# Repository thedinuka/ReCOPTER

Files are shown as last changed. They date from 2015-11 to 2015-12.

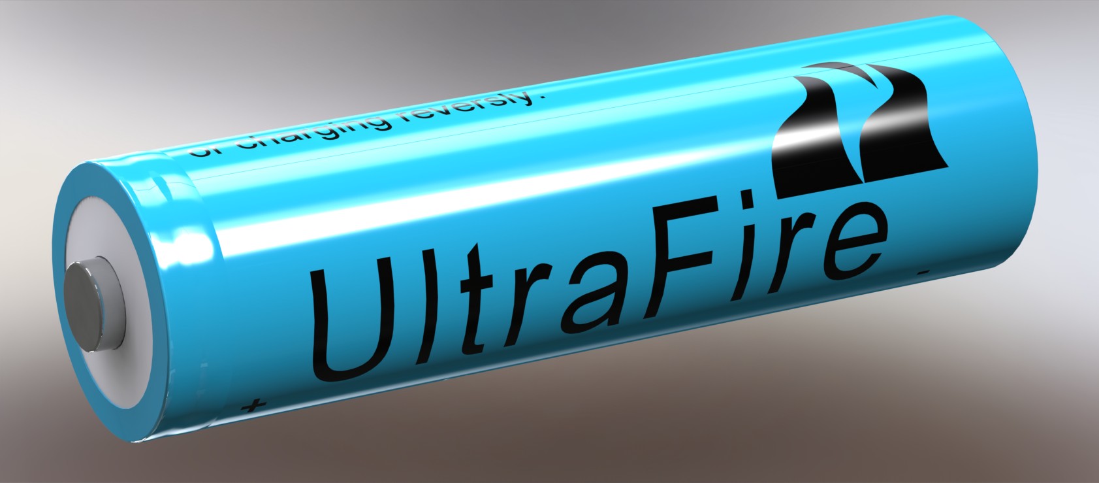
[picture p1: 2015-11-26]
Hardware/Frame/CAD/Parts/ultrafire-18650-2400mah-batteries-1/18650LithiumBatt_Render2.JPG

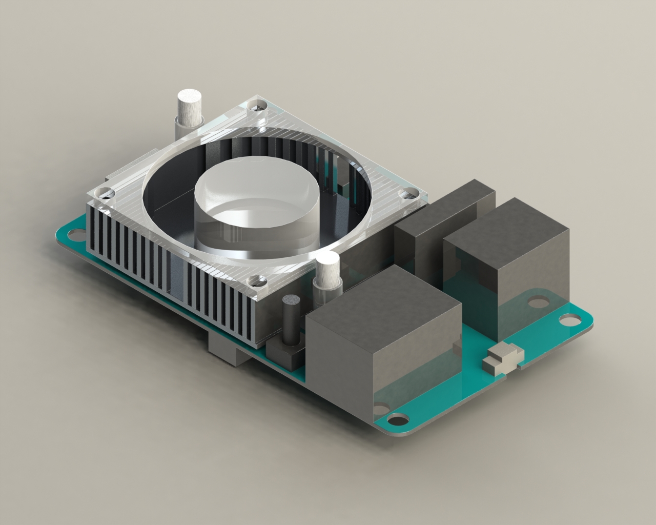
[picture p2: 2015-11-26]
Hardware/Frame/CAD/Parts/Odroid U3/Renderings/odroid-u3.JPG

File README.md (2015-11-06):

# ReCOPTER
Source files for the ReCOPTER paper published in ACRA 2015

If you make use of the material here, please cite the following paper, a copy of which is provided here.
Dinuka Abeywardena, Paul Pounds, David Hunt, and Gamini Dissanayake. Design and Development of ReCOPTER: An Open source ROS-based Multi-rotor Platform for Research. Australasian Conference on Robotics and Automation (ACRA) 2015.

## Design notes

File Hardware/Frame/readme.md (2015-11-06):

This folder contains the CAD models and other relevant design files for the frame of ReCOPTER version 1 as described and illustrated in the ACRA paper.

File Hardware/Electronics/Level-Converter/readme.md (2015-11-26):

Schematics and board files for the level converter board used to communicated between the Pixhawk and the Odroid U3.

The schematics and boad files were prepared using the open source electronics design automation suite KiCad. KiCad is available for download at http://kicad-pcb.org/

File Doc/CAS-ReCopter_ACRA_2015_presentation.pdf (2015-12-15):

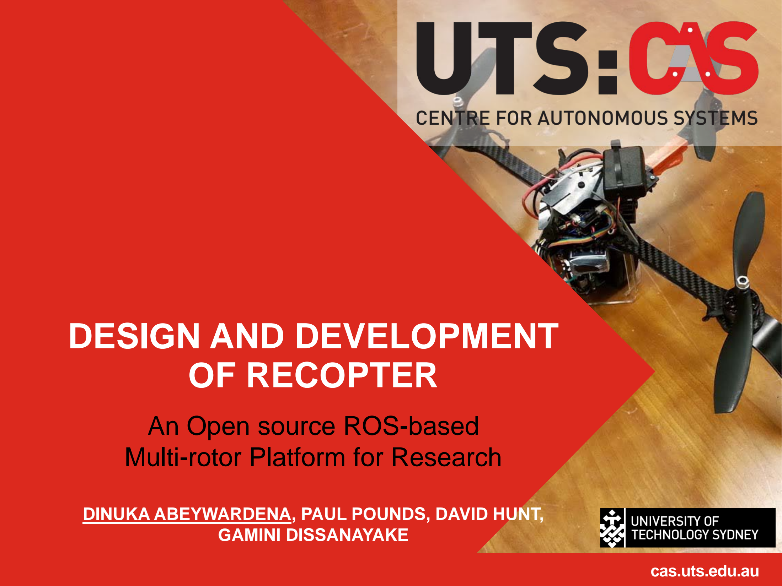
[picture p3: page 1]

# DESIGN AND DEVELOPMENT OF RECOPTER

cas.uts.edu.au

## An Open source ROS-based Multi-rotor Platform for Research

DINUKA ABEYWARDENA, PAUL POUNDS, DAVID HUNT, GAMINI DISSANAYAKE

# MOTIVATION

## Want a UAS to conduct multi-copter research?

## Buy a COTS platform

Expensive
Proprietary hardware and software
Lead time for replacements (specially in Australia!!)

## Build one from Scratch

Time consuming
Can be expensive as well
Requires a diverse skill set

# MOTIVATION

## Want a UAS to conduct multi-copter research?

## Build one based on a proven open source blueprint

Fully customizable HW and SW
Minimum design iterations
Less expensive than COTS Research UAS Easily repairable
Quicker and Easier to build

# APPROACH

Evaluate the state-of-the-art
Evaluate some of the commonly used multi-copter platforms for research
Identify shortcomings & propose improvements Propose design specifications for “researcher friendly” multi-copter design
Design, implement and test and improve Provide a blueprint for the novel design
Build and test multi-copters according to the blueprint Disseminate
Publish results
Open-source the design

# EVALUATE THE S-O-T-A

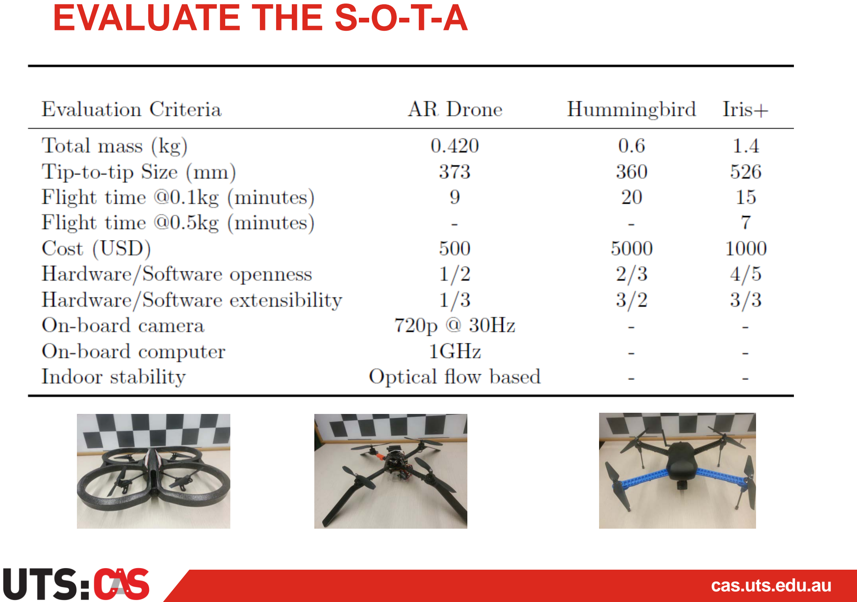
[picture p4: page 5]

# DESIGN SPECIFICATIONS

Criteria | Condition
MTWO | < 2kg
Tip-to-tip size | < 500mm
Max Payload | > 0.5kg
Flight time (0.1kg payload) | > 30 minutes
Flight time (0.5kg payload) | > 20 minutes
Cost | < 1500USD
Openness | Fully open source HW & SW
Extensibility | Modular HW, Standard SW + interfaces
Indoor Stability | Either through optical flow or Tags

# DESIGN PROCESS – FRAME

< ~ 8 inches

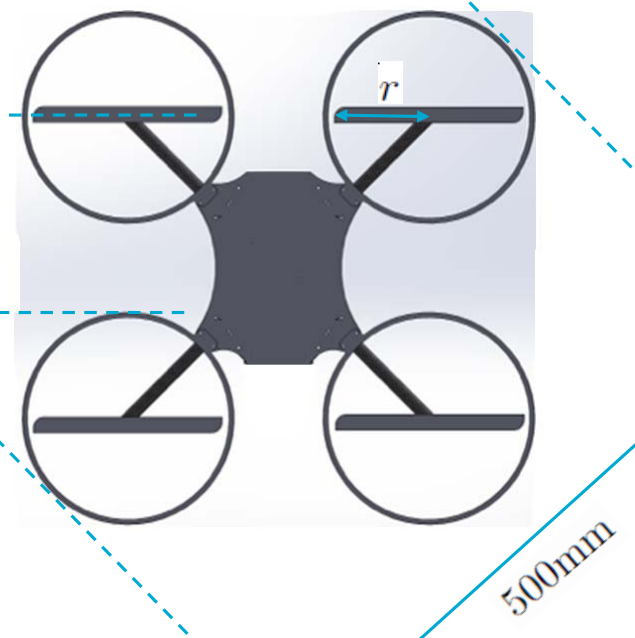
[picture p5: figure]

COTS propeller
options

# DESIGN PROCESS – THRUSTERS AND BATTERY SELECTION

Propellers – T-Motor Carbon Fiber (6, 7, 8 inches)

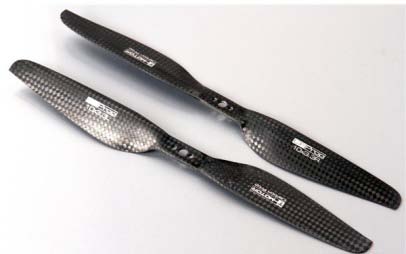
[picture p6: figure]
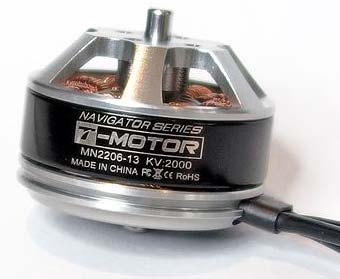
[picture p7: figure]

Motors – Matching T-Motor motors capable of providing at least 5N thrust with any one of the selected propellers (MN 2206 and MT2208)

Batteries – high discharge Li-Ion

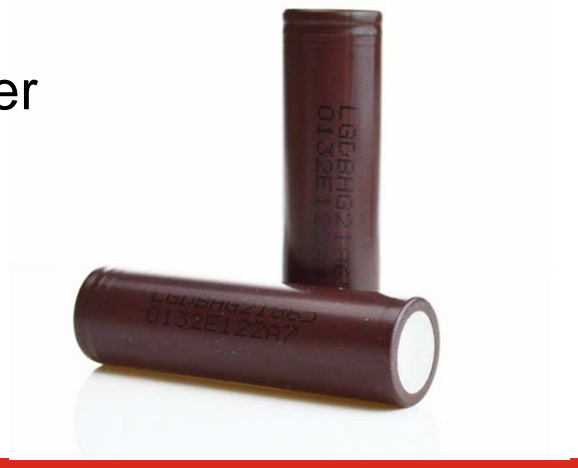
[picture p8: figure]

(compatible configurations with selected Motor/Propeller combinations include 2S2P, 3S2P, 3S3P, 4S3P)

# DESIGN PROCESS – THRUSTERS AND BATTERY COMPARISON

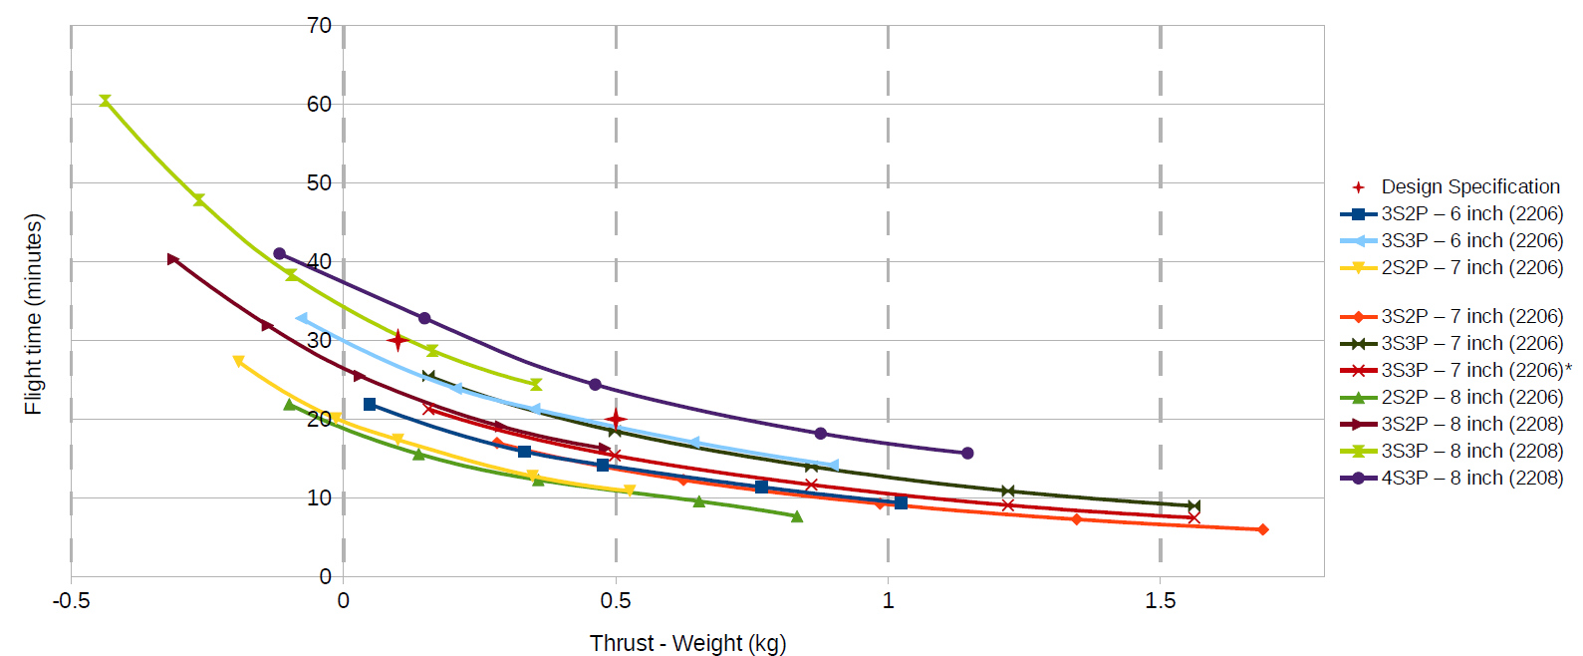
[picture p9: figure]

Data from experimental results obtained from http://www.rctigermotor.com

# AVIONICS + SOFTWARE

Auto-pilot – Pixhawk with native Pixhawk flight stack

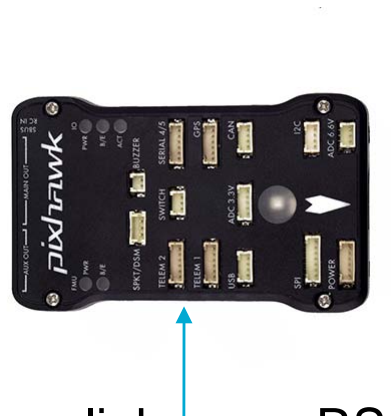
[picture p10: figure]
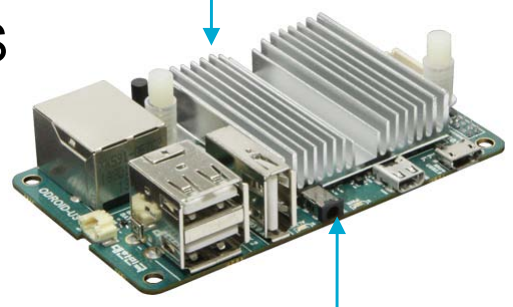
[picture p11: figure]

On-board Computer – Odroid U3* with ROS + MAVROS

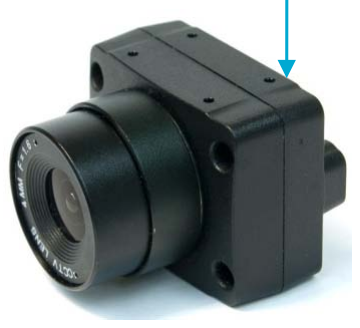
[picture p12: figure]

On-board Camera – Point grey Firefly

mavlink over RS-232

USB 2

# PUT IT ALL TOGETHER – RECOPTER V 1

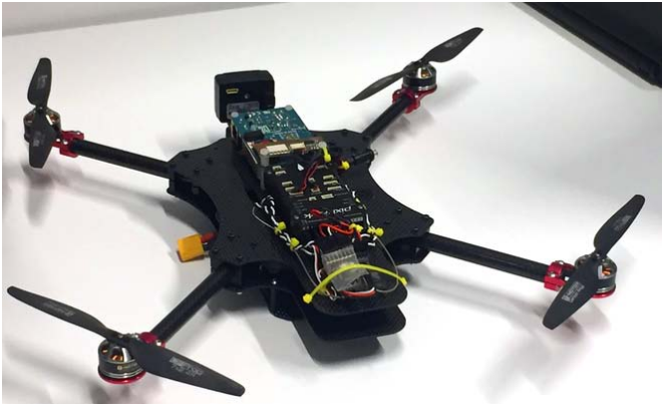
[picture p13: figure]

# FINAL SPECIFICATIONS

Criteria | Proposed | Achieved
Dead Weight | < 1kg | 1.03kg (3s3p)
MTWO | < 2kg | 2.5kg
Tip-to-tip size | < 500mm | 500mm (7 inch prop)
Max Payload | 0.5kg | 1.0kg
Flight time (0.1kg payload) | > 30 minutes | 24 (with 2.5Ah batteries)
Flight time (0.5kg payload) | > 20 minutes | 13.5 (with 2.5Ah batteries)
Cost | < 1500USD | ~1200USD (including on-board computer and Camera)
Openness | Fully open source HW & SW | Pixhawk, Odroid, ROS
Extensibility | Modular HW, Standard SW + interfaces | Modular frame, ROS+mavros
Indoor Stability | optical flow or Tags | AR Tags

# INDOOR STABILITY

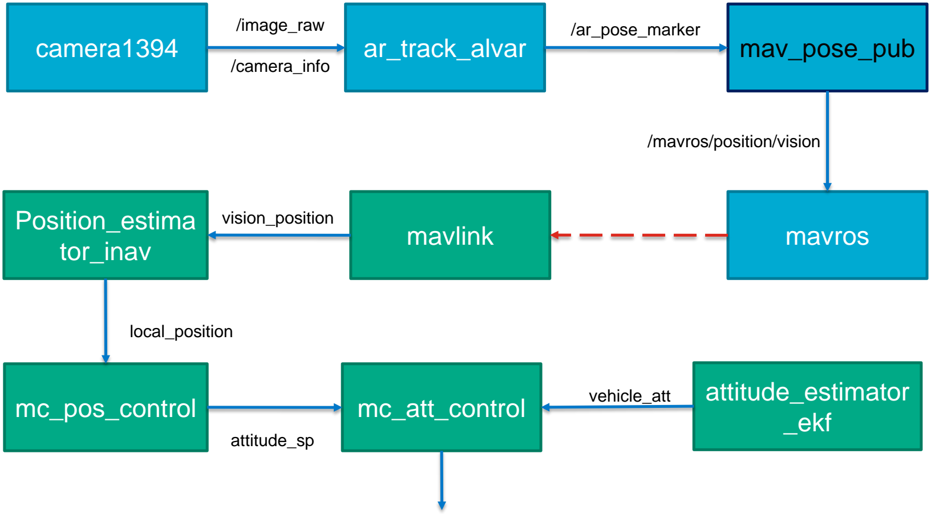
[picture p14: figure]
camera1394; ar_track_alvar; mav_pose_pub; mavlink; mavros; mc_pos_control; attitude_estimator; _ekf; Position_estima tor_inav; mc_att_control; /image_raw; /camera_info; /ar_pose_marker; /mavros/position/vision; vision_position; local_position; attitude_sp; vehicle_att

Actuator control signals

# OPEN SOURCING

# github.com/thedinuka/ReCOPTER

## - Hardware – Cad files for frame v1, Electronics - Complete parts list with approx cost and where to buy - Paper and presentation - Software components are already open source

## To Do: Build Guide?

# FUTURE - RECOPTER V2

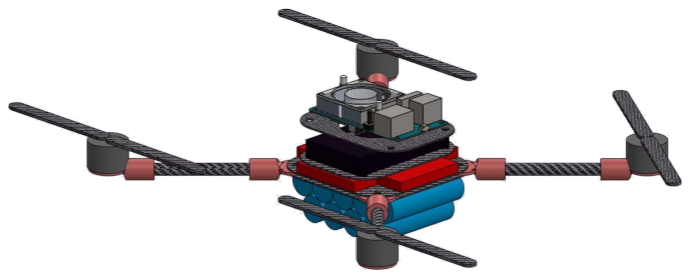
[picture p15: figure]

Increased modularity Decreased dead weight Simplified frame design

# FUTURE - RECOPTER V2

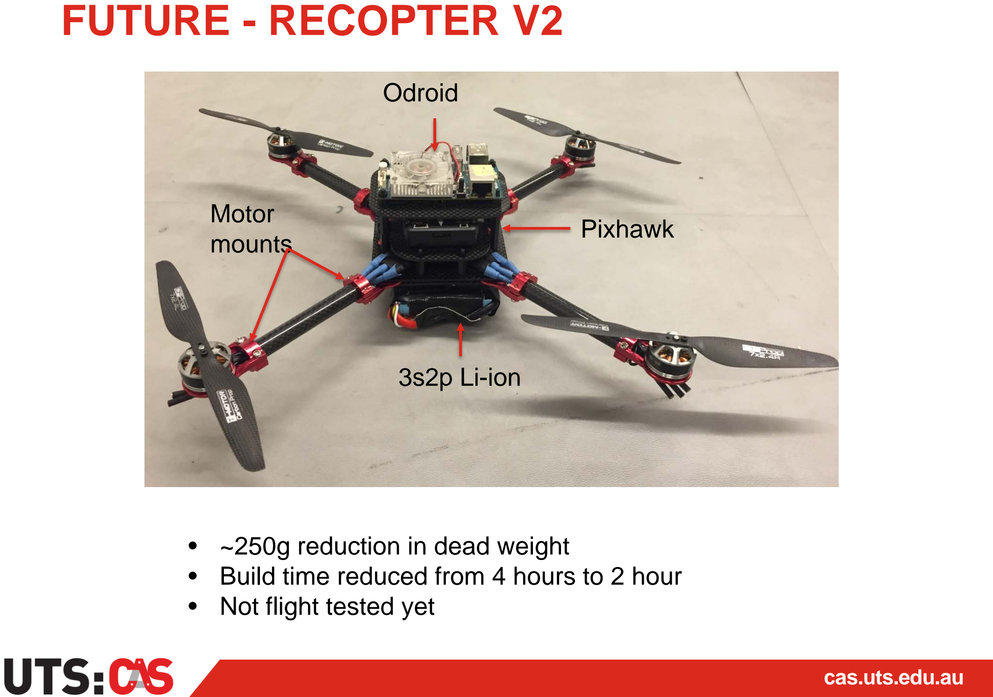
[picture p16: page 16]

Odroid

Pixhawk

3s2p Li-ion

Motor
mounts
- ~250g reduction in dead weight
- Build time reduced from 4 hours to 2 hour
- Not flight tested yet

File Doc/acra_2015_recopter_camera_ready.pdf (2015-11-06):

## Design and Development of ReCOPTER: An Open source ROS-based Multi-rotor Platform for Research

Dinuka Abeywardena ¹∗
, Paul Pounds ²

, David Hunt ¹ and Gamini Dissanayake ¹ 1 Centre for Autonomous Systems, University of Technology, Sydney, Australia 2 Robotics Design Lab, University of Queensland, Brisbane, Australia {Dinuka.Abeywardena, David.Hunt, Gamini.Dissanayake}@uts.edu.au Paul.Pounds@uq.edu.au

Abstract

Selection of multi-rotor aircraft systems for robotics research is a trade-off between competing objectives. While Commercial Off The Shelf systems are fast to set up and provide a ready-made platform, they often lack complete documentation and have limited extensibility for allowing researchers to modify them for scientific work. Conversely, developing an aircraft from the ground up is labour intensive and time consuming, and requires substantial experience to ensure a satisfactory result. This paper ranks common robotic multi-rotor aircraft used in research against several criteria for openness, extensibility and performance. We propose a standard platform using open components and an open-source design, specifically geared to the needs of the research community.

### 1 Introduction

Multi-rotor Unmanned Aerial Vehicles (UAV) have gained significant popularity among both the research and hobbyist communities due to their manoeuvrability, simplicity and low cost. Research conducted using multirotor aerial vehicles belong to two main categories: research that advances the abstract capabilities of the platform itself, and research that employs those capabilities to perform a specific task. Examples of first category include developing multi-rotors capable of aggressive flying and perching [Mellinger et al., 2012], grasping [Mellinger et al., 2013], robustness to wind disturbances [Waslander and Wang, 2009] and many instances of novel state estimation algorithms [Abeywardena et al., 2013], [Mahony et al., 2012]. Examples of the second category include the use of multi-rotor aerial vehicles for indoor exploration [Achtelik et al., 2008], infrastructure inspection [Sa and Corke, 2014] and robotic construction [Lindsey et al., 2011].
The principal features of a UAV are its structure, propulsion, stability and guidance [Pounds and Singh,

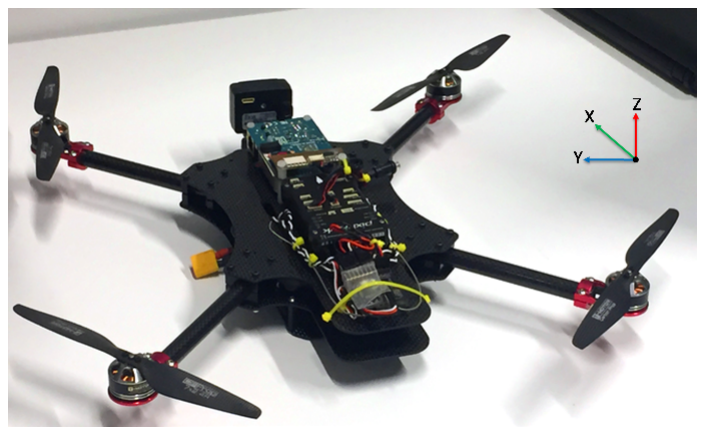
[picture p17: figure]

Figure 1: Proposed open-source multi-copter with autopilot, on-board computer and smart camera.

2013] — all of which are essential for conducting research using a multi-rotor platform. While the specific hardware and software needs may vary depending on the exact research questions being addressed, it is possible to identify a common set of desirable features for multirotor aerial vehicles, if they are to be useful as research platforms. These features include open-source and easily extensible hardware and software, low cost, minimum set-up time, ease of repair and reasonable flight time. There are two options available to a robotic researcher wanting to employ a multi-rotor aircraft as a research platform. First is to purchase one of many Commercial Off The Shelf (COTS) aircraft available in the market today. However, only a few of them, such as the research line of multi-rotor UAVs from Ascending Technologies GmbH, have been designed with the needs of robotics researchers in mind. Most COTS multi-rotor platforms focus on ease of use and payload characteristics, with little or no attention to features such as openness and extensibility. The second option is to design and build multi-rotor platforms in-house to suit the specific needs of the research being conducted, either from scratch or from using COTS parts. While this approach is appealing due the flexibility it offers it is also time consuming and expensive due to the number of iterations and prototypes required to perfect the design.

Our goal is to assist the robotic researcher with both of the above options. Specifically, we aim to provide a framework for multi-rotor platform selection, and a blueprint for an open-source alternative platform specifically targeting the needs of the robotics research community. This is achieved through two key contributions that are detailed in this paper. First, we identify a set of evaluation criteria based on the requirement of aerial vehicle researchers and then use the said criteria to compare three of the most commonly used COTS multi-rotor research platforms. Second, we use the same evaluation criteria as design specification to propose a multi-rotor configuration that can be constructed in a straightforward manner using easily sourced hardware and software components. We have built and tested several multirotor platforms according to this configuration and report on one such instantiation so that other researchers are able to use the same configuration to assemble platforms according to their specific needs, while minimising the design iterations and costs. Whenever possible, we employ open-source hardware and software components to ensure that other researchers interested in building in-house multi-rotor platforms can replicate our designs with minimum effort.
This paper is organized as follows: In section 2 we present our evaluation criteria and in section 3 we use this criteria to compare three of the most common COTS multi-rotor research platforms. In section 4 we propose our novel configuration based on the same evaluation criteria. Section 5 provides details on experimental flights of a multi-rotor platform constructed according to the proposed design and section 6 details an example application of the platform to demonstrate the utility of openness and extensibility of the design. Finally section 7 concludes the paper with a summary of the contributions and future research directions.

### 2 Evaluation Criteria

The key utility aspects of a multi-rotor unmanned aerial system can be decomposed into:

- Platform performance
- Economics and logistics
- Openness and extensibility.

This section details the importance of these aspects for research. Note however that the criteria identified here are by no means an exhaustive set. Depending on the specific sub domain of multi-rotor research, there may be other features that are also important; we aim to identify a generic set of criteria that are relevant to a majority of multi-rotor researchers.

### 2.1 Size, payload, flight time and cost

Flight experiments for multi-rotor research are predominantly conducted in an indoor lab environment with limited flight space. Safe operation with sufficient actuation inside small flight spaces requires small aerial vehicles. Therefore, we postulate that smaller multi-rotor aerial vehicles have a higher utility for conducting research unless the requirement is to specifically analyse the dynamics of large UAV platforms [Pounds and Mahony, 2009]. For most forms of aerial robotic research, the vehicle needs to carry additional sensing, computational or actuation payloads. We define payload as the maximum weight of the components removable from the aerial vehicle while retaining the ability to fly in a useful manner. Strictly speaking, the payload capacity of a given aerial vehicle is only dependent on the maximum thrust it can produce. However, maximum payload capacity can be a misleading indication of the capability of an aerial vehicle; it is necessary to analyse the inverse relationship between the payload and the flight time. To simplify the analysis, here we chose the flight time at a given anticipated payload as our evaluation criteria. Considering the sensing and computational payloads commonly used in multi-rotor research, we define two payload categories as representative. For research involving inertial or monocular vision sensing we define a payload class of 0.1 kg, which could include a small embedded computer and storage for data logging in addition to the sensors. For research involving other bulkier sensing modalities such as LiDAR or depth cameras we define a payload class of 0.5 kg. The evaluation criteria are thus the flight time at 0.1 kg and 0.5 kg payloads. Cost of the aerial platform is obviously a key concern for researchers with limited resources. To enable a fair comparison of the different COTS platforms, cost of the not just the aerial platform itself, but also the complete system including the radio transmitter, receiver, telemetry, spare battery and a reasonable set of other spare parts should be considered¹

### 2.2 Open and extensible hardware and

software

Conducting multi-rotor research often requires modification or extensions to the hardware and software components of the aerial vehicle. For example, evaluating novel control or estimation algorithms require software modifications but adding new sensors require both hardware and software extensions. An effective way to facilitate such modifications is to only employ open source hardware and software components. Software has a long

1While dependent on application, we consider a reasonable set of spare parts to include a pair of extra motors, a pair of ESCs and a replacement set of propellers

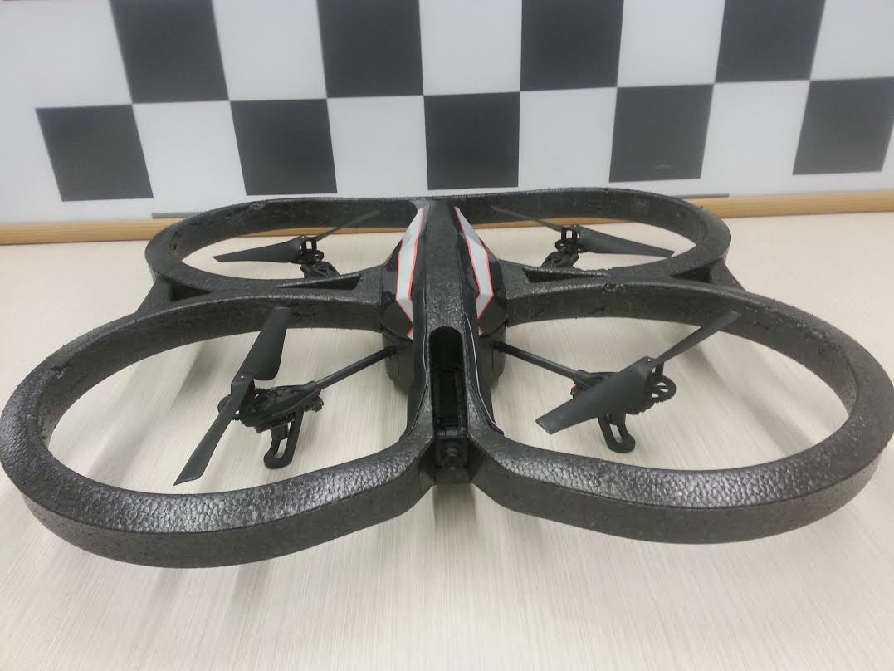
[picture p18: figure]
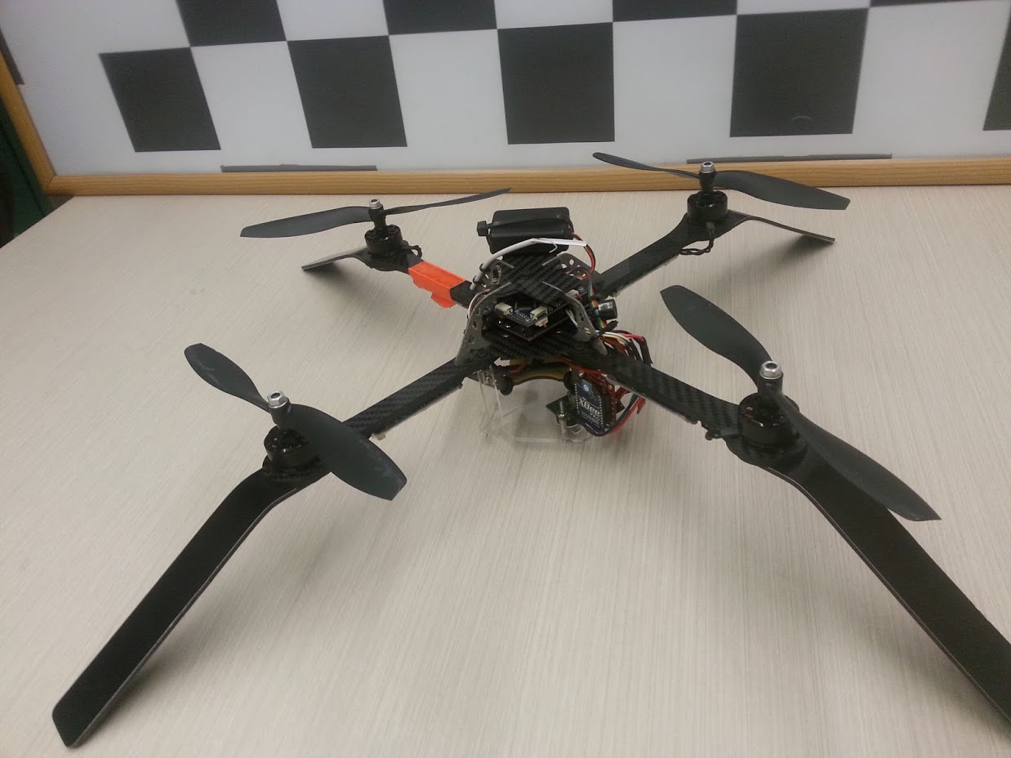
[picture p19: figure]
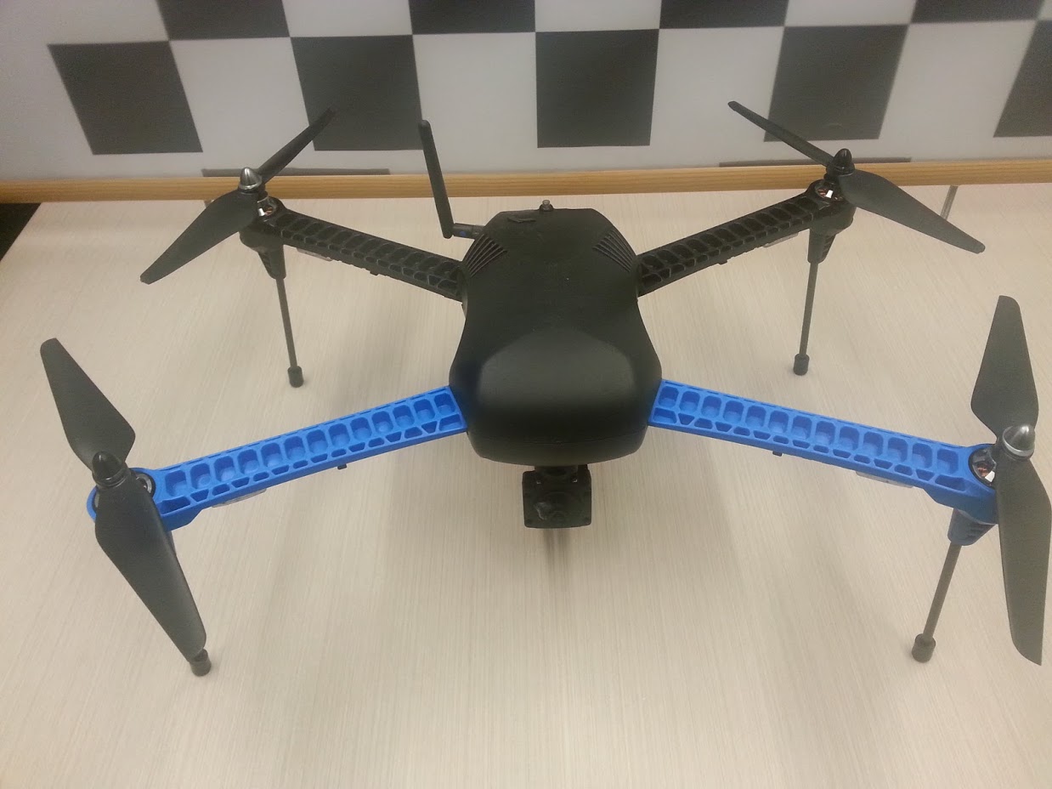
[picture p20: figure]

Figure 2: Common platforms: (a) Parrot AR Drone 2.0 (b) Ascending Technologies Hummingbird (c) 3D Robotics Iris+.

culture of open source licensing that enables a third parties to use and modify it for non-commercial purposes. More recently, hardware source files have also been published under permissive licenses, including frame components and also the schematics and board files of electronic modules being used. While silicon designs of integrated circuits and other discrete components could also be available under open source licenses, the resources required to fabricate them put them beyond the reach of most researchers. Instead, their utility is measured by the availability of technical data sheets and APIs that enable a researcher to exploit their functionality. Openness of the hardware and software does not guarantee the ability for a third party to extend and modify the platform to suit their needs. For example, some platforms may provide the source code of their control algorithms but not an interface to reprogram the autopilot executing the said code. Some other platforms may be accompanied with the design files for the frame components but might not have the necessary modularity to modify a specific part of the frame. Also related to extensibility is the availability of sufficient documentation for both the hardware and software.
To facilitate a quick comparison between different COTS platforms, we grade their openness and extensibility in hardware and software separately on a scale of 0-5, where 5 is the most open or extensible. We recognise that grading openness and extensibility is inherently subjective. We provide information on specific components of each platform that are not open-sourced or not easily extensible in the following section.

### 3 Comparison of COTS multi-rotor

research platforms

Numerous COTS multi-rotor platforms have been used by various aerial vehicle research groups around the world. Of these, we selected two of the most common platforms for comparison, based on an informal survey of the 100 most-cited multi-rotor research papers published between 2010 and 2015 on IEEE Xplore: the AR Drone by Parrot Inc. and the Hummingbird by Ascending Technologies GmbH. We also selected the Iris+ by 3D Robotics Inc. which features many characteristics required of a multi-rotor research platform. Even though the Iris+ has not been popular among robotics researchers, its Pixhawk autopilot is extremely popular and including Iris+ in the comparison enables us to broaden the spectrum of multi-rotor features being evaluated.
Table 1 presents an overview of the COTS platforms features, along with the open source design proposed in section 4. A detailed discussion of these features are presented next.

### 3.1 AR Drone

AR Drone²
is a relatively inexpensive quadrotor platform intended as an easy to use toy aerial vehicle targeting the hobbyist community (see Fig. 2 a). Its tip-to-tip size is 373 mm and weight is 0.455kg. It has a hover flight time of about 9 minutes with 0.1kg of payload but is unable to take-off with a 0.5kg payload. The total cost for a the system is about 500USD.
The AR Drone is pre-equipped with two low resolution cameras and a downward pointing sonar in addition to the standard IMU sensor package. The auto-pilot and sensor driver binaries exist on an on-board Linux computer that can execute custom binary files as well. However, the source code for the auto-pilot and sensor drivers are closed source and therefore accessing sensor measurements or modifying the auto-pilot behaviour is not trivial. AR Drone makes the sensor data available on a separate Ground Station Computer (GSC) via an API that also enables sending high-level navigation commands to the auto-pilot. However, the data connection between the GSC and the AR Drone is wireless (WiFi, IEEE 802.11b/n) and the limited range and delay associated with such networks limits the usefulness of the API for robotic research where real-time sensing and control is a requirement. Design files for neither the frame components nor the avionics are open-source so extending

2There are two available versions of the AR Drone and here we refer to AR Drone 2.0

Evaluation Criteria | AR Drone | Hummingbird | Iris+ | Proposed
Total mass (kg) | 0.420 | 0.6 | 1.4 | 1.03
Tip-to-tip Size (mm) | 373 | 360 | 526 | 500
Flight time @0.1kg (minutes) | 9 | 20 | 15 | 30
Flight time @0.5kg (minutes) | - | - | 7 | 20
Cost (USD) | 500 | 5000 | 1000 | 1000
Hardware/Software openness | 1/2 | 2/3 | 4/5 | 5/5
Hardware/Software extensibility | 1/3 | 3/2 | 3/3 | 5/5
On-board camera | 720p @ 30Hz | - | - | VGA @ 60Hz
On-board computer | 1GHz | - | - | 1.7GHz Quad-Core
Indoor stability | Optical flow based | - | - | AR Tag based

Table 1: Comparison of the COTS and proposed multi-rotor platforms. Openness and extensibility measures range from 1 - 5 where 5 is the most open/ extensible.

the functionality of AR Drone is also non-trivial.
Apart from its low cost, the main advantage of using the AR Drone for robotic research is its ability to perform stable indoor flights with minimum user input. This is achieved by combining the optical flow data from the downward pointing camera and the distance to the ground measurements from the sonar to construct a velocity estimate of the platform which is then used in a closed-loop controller.

### 3.2 Hummingbird

The Hummingbird is part of a research specific line-up of multi-rotor platforms from Ascending Technologies GmbH (see Fig. 2 b). Its tip-to-tip size is 360 mm and weighs 0.6kg. It has a hover flight time of approximately 20 minutes with 0.1kg payload but is unable to carry a 0.5kg payload. Other higher-end Ascending Technologies platforms are advertised as being capable of up to 14 minutes of flight time with 0.6kg payload. The total cost of the full system (with no additional sensors or computing apart from the basic configuration) is approximately 5000USD.
The basic version of the Hummingbird has two on-board 32-bit ARM processors out of which one is reserved for real-time low-level control of the platform. The firmware on the low-level processor is closed source and moreover it cannot be reprogrammed. The high-level processor can be programmed by the user and has access to all in-built sensor data streams and command interfaces of the low-level processor. Adequate documentation on programming the high-level processor and its communication interfaces are provided as well as the ability to add a selected set of new sensors. However, design files for neither the frame components nor the avionics are open-source so adding custom functionality beyond the options provided by the manufacturer is non-trivial. Also, the software architecture adopted for the high-level processor is not that of a modular real-time operating system, thus complicating the implementation of multiple firmware modules on-board the platform. For on-board implementations of more complex algorithms, the Hummingbird can be equipped with an optional Intel Atom computing board. Various additional sensing modalities such as cameras and LiDARs can be connected and used with the computing board.

### 3.3 Iris+

Iris+ is a ready-to-fly quadrotor platform by 3D Robotics Inc. featuring the open-source Pixhawk flight controller (see Fig. 2 c). Its tip-to-tip size is 526 mm and weighs 1.4kg. It has a hover flight time of about 15 minutes with 0.1kg payload and about 7 minutes with 0.5kg. The total cost of the full system is about 1000USD. The key differentiator between the Iris+ and the other COTS platforms discussed above is the openness and extensibility of the Pixhawk auto-pilot hardware and the Pixhawk flight stack. Pixhawk hardware is based on a 168 MHz Cortex-M4F processor and features multiple connectivity options and a full suite of in-built inertial sensors. The hardware is fully open-source (including the schematic and board layout) and multiple additional sensors (also open-source) are supported by default. The Pixhawk processor can be easily programmed with custom firmware but two mature open-source flight stacks are available to free the user from the burden of developing auto-pilot firmware from scratch. These flight stacks — the native Pixhawk flight stack and the APM flight stack — have been tested and verified by thousands of users. The Pixhawk flight stack features a real-time operating system and a modular software architecture [Meier et al., 2015] making it straightforward to extend the functionality of the auto-pilot.
One disadvantage of the Iris+ compared to the AR Drone and the Hummingbird is the lack of a readily available on-board computer to perform high-level tasks such as sensor fusion, localization and mapping. Even though the Pixhawk and APM flight stacks both support MAVLink [Meier et al., 2013] - a standardized protocol for auto-pilots to communicate with the external world
- an off-the-shelf on-board computer that can interface with the Pixhawk via MAVLink protocol is not readily available. Also, even though the Iris+ frame provides many options for mounting and interfacing with other sensors, the design files for the fame components are not available, thus reducing the extensibility of the platform.

### 4 Proposed Design

It can be seen from Table 1 that none of the commonly used platforms excel in all areas. For this reason, we seek to outline the structure of a multi-rotor configuration particularly targeting aerial vehicle research. We specify the major features of the design including the frame, thrusters, avionics and software.

### 4.1 Design specifications

We aim for a minimum flight time of 30 minutes with 0.1 kg payload and 20 minutes with 0.5 kg payload. We specify the maximum tip-to-tip size to be 500 mm. The upper limit on total cost is to be 1500 USD. Additionally, we impose a Maximum Take-off Weight (MTOW) of 2 kg, motivated by the impending weight-based Unmanned Aerial Systems (UAS) classification by the Australian regulator, CASA, in which it is proposed to deregulate UAS with a MTOW less than 2kg. Similar classifications are now being adopted or proposed in many other countries including the U.S. and Canada. Perhaps the most important of the evaluation criteria of section 2 were the openness and extensibility. For the proposed design, we specified that all non-trivial hardware and software components to be open-sourced under a license that is at least as permissive as to allow share and modify for non-commercial purposes. This specified that where possible, all non-trivial off-the-shelf modules be sourced with a license that is at-least as permissive as the Creative Commons Attribution-NonCommercial-ShareAlike (CC BY-NC-SA) license and be released to the public without violating their current licenses. This also specified that any hardware or software modules that were developed in-house to be released under the same CC BY-NC-SA license.
Openness is a necessary, but not sufficient, condition for extensibility. Moreover, extensibility is a more difficult criteria to objectify than openness and depends largely on the skill level and experience of the researcher. In general, extensibility stems from modularity and adherence to standards. For the proposed design, we specified that hardware and software be preferably modularized and that all software components should make use of standard packages that are commonly used among robotics researchers.

### 4.2 Frame, thrusters and battery

The design specifications which were set forth previously called for a tip-to-tip size of 500mm and a minimum flight time of 30 minutes. This is a significant design challenge especially considering the fact that COTS multi-rotor platforms (for both research and commercial purposes) of similar scale have flight times in the range of 10 - 15 minutes. To achieve this specification, we needed to identify the most efficient commercially available motor - propeller - battery combination that is also within the frame design parameters and to evaluate whether that combination was able to provide the required flight time. If not, then a redesigning of one or more components of the motor - propeller - battery combination would be required.
The first question to answer in the thruster selection process is the number propellers to use and in which configuration. The available options are 3 propellers in tricopter configuration [Zou et al., 2012], 4 propellers in a quadcopter configuration [Pounds et al., 2006] or triangular quadrotor configuration [Driessens et al., 2013], 6 propellers in a hexacopter configuration [Baranek and
Solc, 2012 ˇ | ] or twin Y configuration [Czyba et al., 2015]
and 8 propellers in a octocopter configuration or twin quadcopter configuration. Out of these, we omit the tricopter and triangular quadrotor configurations due to their added mechanical complexity. The 500mm upper limit on tip-to-tip size means that designed multi-rotor should be fully contained within a circle of 500mm radius. The most efficient configuration will be the one which employ most of the area inside that circle for thrust production, with the least amount of propeller overlap. This can be solved by posing it as a variation of the “circle packing problem”, with the objective of optimizing the area of non-overlapping, constant size, n number of circles inside a unit circle with n ∈ [3, 4, 6, 8]. Optimum solution is reached with n = 4 [Kravitz, 1967], making the quadrotor configuration the most efficient — a hexacopter and octocopter would require 1.5 per cent and 5.5 per cent more power to hover, respectively.
| The 500mm tip-to-tip constraint also allows us to iden-
tify a suitable size range for propellers. Griffeths and Leishman reasoned that to be free of inter-propeller turbulence, the tip-to-shaft clearance of small scale propellers should be at least √
| 2r where r is the propeller
radius [Griffiths and Leishman, 2002]. This constraint limits the available COST propeller diameter sizes to 6, 7, 8 inches³
| . At this size range, both Carbon Fiber
(CF) and plastic propellers are commonly available in

3
8
| 00 propellers results in slightly larger tip-to-tip dimen-
sion than 500mm.

the market. We decided to make use of the CF propellers as their stiffness lends to added efficiency due to less propeller twist under load. We selected CF propellers from T-Motor to evaluate, in three different sizes: 6 × 2

00, 7 × 2.4

00 and 8 × 2.7

00
Given the requirement for a quadcopter configuration with a MTOW of 2kg, each propeller should produce at least 4.9N of thrust. This thrust requirement, coupled with the selected propellers, limits the number of available COTS motors options. We identified two T-Motor motors that are able to match the thrust requirement with at least one of the 6, 7, 8 inch propellers: the MN2206 and MT2208, with KV values of 2000 rpm/V and 1100 rpm/V respectively. Motors with significantly higher KV values than that have insufficient torque to be able to drive the selected propellers. Those with significantly lower KV values are unable to maintain sufficiently speed for the required thrust.
There are two suitable battery technologies available for the energy density and discharge rate requirements of multi-rotors: Lithium-Polymer and Lithium-Ion. Lithium-Polymer batteries have less energy density than Lithium-Ion batteries but are the most popular in the multi-rotor community because of their higher discharge rates. A new category of Lithium-Ion batteries that have discharge rates on par with Lithium-Polymer batteries have been introduced to the market by Samsung and LG. These include the 2.5Ah Samsung INR18650-25R which is rated for 22A continuous discharge current and the 3Ah LG 18650HG2 which is rated for 20A continuous discharge current with energy densities of 209WHr/kg and 234WHr/kg respectively.⁴
The 3Ah LG 18650HG2 is proposed for the configuration due to its higher energy density. These batteries come in individual cells, each with a cell voltage of 3.6v, and need to be stacked together to be able to drive the selected motor-rotor combinations. We assessed the suitability of several different battery configurations to identify the most suitable for each motor-rotor pair. A given battery configuration is denoted here by the xSyP notation, which indicates a battery pack consisting of x individual cells in series and y number of such configurations in parallel, for a total of x × y cells in the pack. We assessed several combinations of the three rotors and two motors considered, with different combinations of battery arrangements. Much of the data required for this empirical analysis are readily available from the manufacturer websites. Here we combine that data with other parameters of our design and present them in a unique way that facilitates an informed selection of the

4
In comparison, the Thunder Power TP2100-3SP+25, which is a high energy density Lithium-Polymer battery rated for 52.5A continuous current and 2.1Ah capacity has an energy density of 156WHr/kg

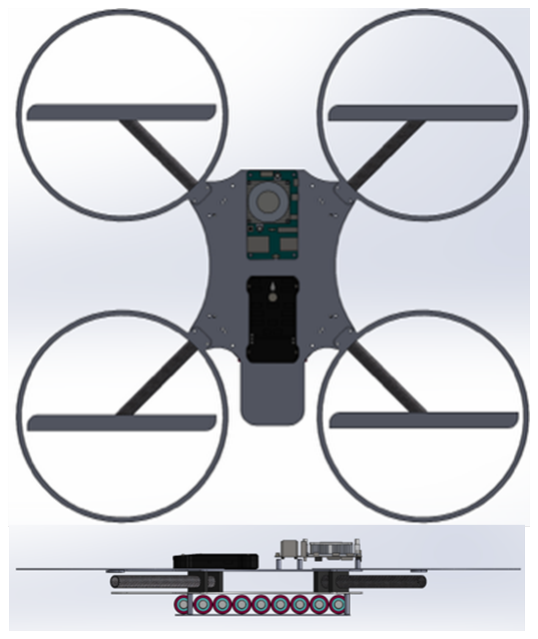
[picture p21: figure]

Figure 4: Proposed frame design. Top: top view. Bottom: side view.

motor, propeller and battery combination capable of providing best flight times at different payloads. The results of the analysis are illustrated in Fig. 3. Details of how the results were generated are given in Appendix A. Fig. 3 illustrates that out of the 11 configurations analysed, only the MT2208 motor equipped with a 8×2.7

00 propeller and powered by a 4S3P battery configuration is capable of exceeding the design specification of 30 and 20 minutes flight times at 0.1kg and 0.5kg payloads, respectively. However, the 8 × 2.7

00 propellers
were not available for purchase at the time and therefore, the next configuration that was closest to the design specification needed to be chosen. Both the 3S3P-7 inch (2206) and the 3S3P-6 inch (2206) configurations had performances slightly lower than the design specifications. Out of these two, the 3S3P-7 inch (2206) configuration was chosen as it had about twice the payload capacity as the 3S3P-6 inch (2206) configuration.

### 4.3 Frame Design

The selected motor-propeller-battery combination, rotor configuration and the tip-to-tip size constraint determines the key physical parameters of the frame design. Other main considerations included the ease of sourcing raw material, ease of assembly and repairability. Considering these, we opted for a simple frame design which makes use of ubiquitous Carbon Fiber (CF) tubes and sheets, as illustrated in Fig. 4. The most complex process of the build is machining of the CF plates to the required shapes, which can be performed using a conventional CNC router. The design files for the frame are released on-line under CC BY-NC-SA.⁵

### 4.4 Avionics

Pixhawk auto-pilot was chosen for the proposed design to satisfy the openness and extensibility design specifi-

5
github.com/thedinuka/ReCOPTER

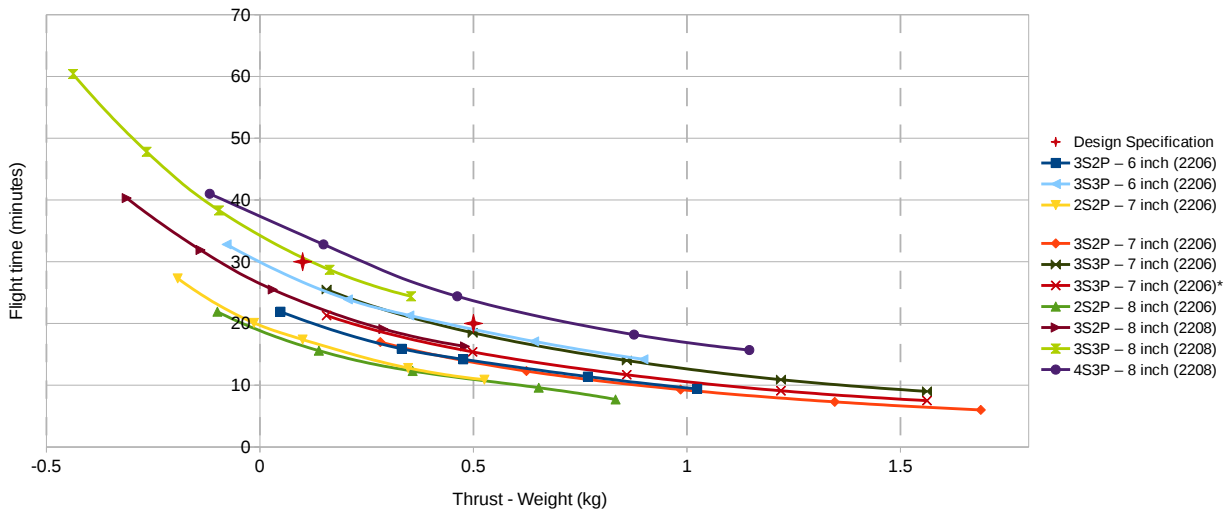
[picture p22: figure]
Design Specification 3S2P – 6 inch (2206) 3S3P – 6 inch (2206) 2S2P – 7 inch (2206); 3S2P – 7 inch (2206) 3S3P – 7 inch (2206) 3S3P – 7 inch (2206)* 2S2P – 8 inch (2206) 3S2P – 8 inch (2208) 3S3P – 8 inch (2208) 4S3P – 8 inch (2208); Thrust - Weight (kg); Flig; ht tim; e (min; ute

Figure 3: | Payload versus flight time curves. | Each curve is labelled using <battery configuration>-
<propeller diameter> (<motor used>) notation. 3Ah single cell capacity was assumed for each curve except for the one marked with ∗ for which 2.5Ah capacity was assumed. X axis represents the thrust (in kg) over and above that which is required for the given configuration to hover. Hover flight time is given by the Y axis intercept of each curve. The right most data point of each curve represents the maximum thrust producible from that configuration.

cation. Schematics and board files of the Pixhawk autopilot hardware are available on-line⁶
| , licensed under the
Creative Commons Attribution-ShareAlike 3.0 Unported (CC BY-SA 3.0).
To improve the hardware and software extensibility, we also incorporated an on-board computer to the proposed design. There are many COTS single board computing platforms available to chose from and considering the power, weight and ease of use, the Odroid U3 by Hardkernel was chosen as the on-board computer. Odroid U3 features a Cortex-A9 Quad-core processor with 2GB main memory and a host of i/o interfaces. Although the actual schematics and board files of the U3 are not provided, documentation diagrams in PDF and JPEG format are available online.
To be useful, the on-board computer needs to communicate with the auto-pilot to receive sensor data and to issue control commands. It is possible for the Odroid U3 to communicate with the Pixhawk via the USB interface. However, communications over USB interfaces incur significant and variable delays that can adversely affect the performance of real-time estimation and control tasks performed on the on-board computer. For this reason, it was decided to make use of the hardware UART interfaces of the U3 and the Pixhawk for communicating between them. To achieve the required voltage level conversion between the two devices a separate PCB was designed, the schematics and board files of which are re-

6https://github.com/PX4/Hardware

leased under the CC BY-NC-SA license. Apart from the level conversion, this board was also used to generate a hardware trigger for the on-board camera.
The proposed design also includes an on-board machine vision camera to facilitate computer vision related research using multi-rotor platforms. In choosing a specific camera model, we focused on three main features; high frame rate, global shutter and external trigger capability. These features are essential for accurate synchronization of the camera images with IMU measurements originating from the Pixhawk. The model selected for the on-board camera was the FMVU-03MTM-CS by Point Grey. This camera features a USB 2 interface for image transfer, a monocular 0.3 Mega pixel sensor and global shutter. The camera supports a maximum frame rate of 60fps, but this maximum can only be reached in continuous trigger mode. The speed at which the camera can be externally triggered depends on the exposure time and through experimentation it was found that a frame rate of about 50fps can be achieved for external triggering while maintaining a suitable exposure for an indoor scene.
Avionics also includes the Electronic Speed Controllers (ESC) required for controlling the BLDC motors. Again, there are many available COTS ESC options and in choosing one we focused on the continuous current rating and the PWM refresh rate. Continuous current rating of the ESC should be above the maximum current drain supported by the motor and as a rule of thumb the

PWM refresh rate should be at least 400Hz. For the proposed design we have chosen the Hobywing XRotor-20A ESC but there are many others that satisfy there criteria. However, it should be noted that the hardware for most COTS ESCs, including the XRotor-20A, are not open source. Usually their firmware is also not open source but some can be programmed with open source ESC firmware (for example see https://github.com/sim-/tgy). If fully open source ESCs are required, then one can make use of the Pixhawk ESC, which is planned to be made available commercially towards the end of 2015.

### 4.5 Software

The software for the propose design consists of two main components: the firmware of the auto-pilot and the software for the on-board computer. In this section, we discuss the available choices given the selected hardware and make use of the design specifications to identify the most appropriate option for the proposed design. There are two options available for the auto-pilot firmware of the Pixhawk: the APM flight stack based on the ArduPilot code base and the native Pixhawk flight stack. Out of the two options, Pixhawk flight stack is more modular and robust as it is based on a real-time operating system known as NuttX. Actual auto-pilot code is implemented as modules that communicate with each other through a subscriber-publisher architecture. This abstracts away the specific details of reading from or writing to of information to peripheral devices such sensors and actuators. A researcher with the need to extend the functionality of the auto-pilot - for example with a new sensing or control algorithm - needs only to subscribe to the topics that carry the required input information and to publish the results to the relevant topics without having to know in detail how the input information is captured or how the output data is made use by other modules. Due to these benefits the Pixhawk flight stack was chosen for the proposed design. Pixhawk flight stack also supports MAVLink, which is a standardized protocol for auto-pilots to communicate with the external world. In this case MAVLink is used to communicate both with the ground station computer and the on-board computer.
The Pixhawk hardware has limited computing power and is not suitable for more high-level sensor fusion, control and planning tasks that are of interest to robotic researchers. Such tasks should be offloaded to the on-board computer. In-order to perform these tasks, the on-board computer needs to provide an easily extensible interface to the researchers to receive and process the data from the Pixhawk and to send commands back to it. To achieve this, the proposed design makes use of the Robotic Operating System (ROS) middleware for the Odroid U3. Architecture of ROS is similar to that of the Pixhawk firmware in that it is based on a subscriber-publisher framework which allows individual modules that makes use of data from other modules to be developed easily. The proposed design makes use of MAVROS, which is a standard ROS package to communicate with devices supporting MAVLink, to establish seamless bi-directional communication with the Pixhawk firmware. The proposed design also makes use of the time synchronization feature of MAVROS to synchronise the Pixhawk and Odroid U3 clocks, thereby enabling precisely timestamped sensor and command messages. With the MAVROS-MAVLink connection and with the time synchronization, the distinction between the firmware modules on Pixhawk and ROS packages on the Odroid U3 disappears, allowing the robotics research to implement their algorithms on the much familiar ROS framework instead of on the Pixhawk framework with same level of performance for all but the strict delay sensitive tasks.
The source code of the core components of ROS including the MAVROS package and the entire Pixhawk flight stack are available under the BSD license. Other third party ROS packages may have different licenses.

### 5 Final Specifications and Flight tests

A quadcopter platform incorporating all of the components of the proposed design is illustrated in Fig. 1. The key parameters of the platform are presented in Table 2. This platform with different payloads was employed to perform flight tests in an indoor arena to evaluate how it conformed to the flight time estimates presented in Fig. 3. For all such flights, only the hover flight time was measured, with the quadcopter hovering approximately 1.5m above ground. Each flight was initiated with fully charged battery cells at 4.1V cell voltage and terminated when the cell voltage reached 3V, which is the recommended maximum discharge voltage for the batteries used.
Flight tests conducted with 7 × 2.4

00 propellers
and 2.5Ah Lithium-Ion battery in 3S3P configuration demonstrated a 24 minute flight time with 0.1kg payload and 13.5 minute with 0.5kg payload which are in close agreement with the results presented in Fig. 3 (consider the curve for 3S3P-7 inch (2206)*). This indicates that
a planned future design iteration with 8×2.7 | 00 inch pro-
pellers and 3Ah batteries in 4S3P configuration would be capable of surpassing the flight time specifications identified in section 4.1.

### 6 Application Example - Low Cost

Motion Capture System

This section details how the openness and extensibility of the proposed design can be used effectively in conducting robotics research, taking as example one of the

Parameter | Value
Total mass (kg) | 1.03
Propeller radius (m) | 0.1016
Motor flux linkage coefficient | 0.00478
Propeller thrust coefficient | 0.01079
Propeller torque coefficient | 0.00098
Rotational inertia Ixx (kgm²
) 0.0426
Rotational inertia Iyy (kgm²
) 0.0523
Rotational inertia Izz (kgm²
) 0.0885

Table 2: Frame and aerodynamic parameters of the quadcopter platform constructed according to proposed design.

most common requirements for research involving novel control and estimation techniques in robotics: obtaining ground truth trajectory estimates. We demonstrate how the components of the proposed design can be easily extended to achieve this task without having to resort to expensive external motion tracking systems such as Vicon.
The ground truth trajectory estimation system is based on the open-source an open “ar track alvar” ROS package by Scott Niekum which makes use of Augmented Reality (AR) tags affixed rigidly to the environment. This package was installed on the Odroid U3 and was configured to subscribe to the images from the on-board camera, operating at 30fps. One wall of the flight space was affixed with 63 unique AR tags. The 3D coordinates of tags with respect to the centre of the wall was included in an XML file which the ar track alvar package uses to estimate the coordinates of the body mounted camera with respect to a coordinate frame positioned at the centre of the said wall. These estimates can either be used to derive ground truth states for evaluating novel state estimation algorithms or can be used in a feedback loop to control the position of the aerial vehicle within the flight volume. To achieve the latter, the trajectory estimates are transmitted via MAVROS-MAVLink to the Pixhawk framework, where they are published as ”local position” estimates. A position controller module on the Pixhawk then makes use of those position estimates to control the vehicle position. The flight time experiments described in section 5 were conducted in this manner.

### 7 Conclusion and Future Work

This paper first identified a set of desirable features of multi-rotor aerial platforms for the robotic researcher and evaluated three commonly used off-the-shelf platforms using those features. Having identified that none of the platforms under consideration excelled in all of the areas, we then proposed an open-source multi-rotor configuration which combines the desirable characteristics of the off-the-shelf platforms. This proposed design can be used as a blueprint by the robotic research community for assembling multi-rotor aerial vehicles with minimum design iterations and prototyping. We also presented details of one such instantiation of the proposed design demonstrating its ability to achieve the specifications set forth for the design.
In our future work we intend to improve proposed design, mainly for increased hardware extensibility and endurance. To increase extensibility, we aim to improve the modularity of the frame design so that the “arms” of the design (including the thrusters) can be easily added, removed or replaced with minimum effort. To increase endurance, we aim to reduce the platform weight and make use of the best propeller-motor-battery combination identified in section 4. Our aim in this regard is to achieve 1 hour flight time with 0.1kg payload while still maintaining the tip-to-tip size below 500mm.

A Appendix - Calculating flight times

This Appendix details how the data for Fig. 3 was generated by combining empirical data available from the propeller, motor, battery manufacturers and the parameters of the proposed design.
Thrust produced by the MN2206 and MT2208 motors with different propellers at several different levels of cell voltages and current draw are available from the manufacturer⁷
. However, flight time of a given multirotor platform employing these motor-propeller combinations depends on other factors specific to that design such as the frame weight, battery configuration and battery capacity. Importantly, weight of the batteries account for approximately 50% of the platform weight and therefore, different battery configurations will have significantly different weights. To account for these variations, we focused on “additional thrust” instead of the actual thrust for generating data for Fig. 3. Additional thrust Ta was defined as the difference between the actual thrust and the hover thrust and was calculated as:

Ta = (TMNM) − (mP + mMNM + (NBp × NBs)mB)

where TM is the thrust generate by each motor (in kg), NM is the number of motors in the considered configuration (NM = 4 for a quadcopter), mP is the weight of the platform including the frame and avionics, mM is the weight of the motor being considered, NBs, NBp are the number of battery cells in series and parallel, respectively, and mB is the weight of a single cell battery. The flight time tf for each configuration was calculated using the following equation:

tf =

CBηBNBp
IMNM

7www.rctigermotor.com where CB is the nominal capacity of a single cell battery, ηB is a factor that denotes how much of the battery can be drained without damaging it (ηB = 0.85 for the Lithium-Ion batteries used) and IM is the current draw per motor.

References

[Abeywardena et al., 2013] D. | Abeywardena,
S. Kodagoda, G. Dissanayake, and R. Munasinghe. Improved state estimation in quadrotor mavs: A novel drift-free velocity estimator. Robotics Automation Magazine, IEEE, 20(4):32–39, Dec 2013.
[Achtelik et al., 2008] Markus | Achtelik, | Abraham
Bachrach, Ruijie He, Samuel Prentice, and Nicholas Roy. Autonomous navigation and exploration of a quadrotor helicopter in GPS-denied indoor environments. In Robotics: Science and Systems Conference, June 2008.
[Baranek and Solc, 2012 ˇ | ] Radek Baranek and Frantiˇsek
Solc. Modelling and control of a hexa-copter. In ˇ Carpathian Control Conference (ICCC), 2012 13th International, pages 19–23. IEEE, 2012.
[Czyba et al., 2015] Roman Czyba, Grzegorz Szafranski, Marcin Janik, Krzysztof Pampuch, and Michal Hecel. Development of co-axial y6-rotor uav-design, mathematical modeling, rapid prototyping and experimental validation. In Unmanned Aircraft Systems (ICUAS), 2015 International Conference on, pages 1102–1111. IEEE, 2015.
[Driessens et al., 2013] Scott Driessens, Paul E Pounds, et al. Towards a more efficient quadrotor configuration. In Intelligent Robots and Systems (IROS), 2013 IEEE/RSJ International Conference on, pages 1386– 1392. IEEE, 2013.
[Griffiths and Leishman, 2002] Daniel A Griffiths and J Gordon Leishman. Astudy of dual-rotor interference and ground effect using a free-vortex wake model. Circulation, 2:1, 2002.
[Kravitz, 1967] Sidney Kravitz. Packing cylinders into cylindrical containers. Mathematics magazine, pages 65–71, 1967.
[Lindsey et al., 2011] Quentin | Lindsey, | Daniel
Mellinger, and Vijay Kumar. | Construction of
cubic structures with quadrotor teams. | Proc.
Robotics: Science & Systems VII, 2011.
[Mahony et al., 2012] R. Mahony, V. Kumar, and
P. Corke. Multirotor aerial vehicles: Modeling, estimation, and control of quadrotor. IEEE Robot. Autom. Mag., 19(3):20–32, 2012.
[Meier et al., 2013] Lorenz Meier, JF Camacho, B Godbolt, J Goppert, L Heng, M Lizarraga, et al.

Mavlink: Micro air vehicle communication proto-
col. | Online]. Tillg¨anglig: | http://qgroundcontrol.
org/mavlink/start.[H¨amtad 2014-05-22], 2013.
[Meier et al., 2015] L. | Meier, | D. | Honegger, | and
M. Pollefeys. | PX4: A node-based multithreaded
open source robotics framework for deeply embedded platforms. In Robotics and Automation (ICRA), 2015 IEEE International Conference on, may 2015.
[Mellinger et al., 2012] Daniel | Mellinger, | Nathan
Michael, and Vijay Kumar. Trajectory generation and control for precise aggressive maneuvers with quadrotors. The International Journal of Robotics Research, page 0278364911434236, 2012.
[Mellinger et al., 2013] Daniel | Mellinger, | Michael
Shomin, Nathan Michael, and Vijay Kumar. | Co-
operative grasping and transport using multiple quadrotors. In Distributed autonomous robotic systems, pages 545–558. Springer, 2013.
[Pounds and Mahony, 2009] Paul Pounds and Robert Mahony. Design principles of large quadrotors for practical applications. In Robotics and Automation, 2009. ICRA’09. IEEE International Conference on, pages 3265–3270. IEEE, 2009.
[Pounds and Singh, 2013] Paul E Pounds and Surya PN Singh. Integrated electro-aeromechanical structures for low-cost, self-deploying environment sensors and disposable uavs. In Robotics and Automation (ICRA), 2013 IEEE International Conference on, pages 4459– 4466. IEEE, 2013.
[Pounds et al., 2006] P. Pounds, | R. Mahony, | and
P. Corke. Modelling and control of a quad-rotor robot. Australasian Conference on Robotics and Automation, December 2006.
[Sa and Corke, 2014] Inkyu Sa and Peter Corke. Vertical infrastructure inspection using a quadcopter and shared autonomy control. In Field and Service Robotics, pages 219–232. Springer, 2014.
[Waslander and Wang, 2009] Steven L Waslander and Carlos Wang. Wind disturbance estimation and rejection for quadrotor position control. In AIAA Infotech@ Aerospace Conference and AIAA Unmanned... Unlimited Conference, Seattle, WA, 2009. [Zou et al., 2012] Jie-Tong Zou, Kuo-Lan Su, and Haw Tso. The modeling and implementation of tri-rotor flying robot. Artificial Life and Robotics, 17(1):86–91, 2012.

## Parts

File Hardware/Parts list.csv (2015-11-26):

Item | Description | Qty | Approx Unit Price (AUD) | Total (AUD) | Comments | Where to buy
Frame
200×300×1.5mm Carbon Fiber sheet | CF sheets for frame plates | 3 | 25.00 | 75.00 |  | http://www.ebay.com.au/itm/261498029200
12MM OD X 10MM ID X 500MM Carbon fiber tube | CF tubes for frame arms | 4 | 9.00 | 36.00 |  | http://www.ebay.com.au/itm/390907531073 (this item includes 4 tubes, So you only need one of these)
Quadcopter Motor Mount Holder for 12mm Carbon Fiber Tube | Motor mount | 4 | 5.00 | 20.00 |  | http://www.ebay.com.au/itm/271455704404
Hex M-F Spacers/ Screws/ Nuts/ Standoff Assorted Kit |  | 1 | 8.00 | 8.00 |  | http://www.ebay.com.au/itm/271951666962
Thrusters
LG 18650HG2 3.6V 3000mAh Rechargeable Li-ion Batteries | Li-ion Batteries | 12 | 7.10 | 85.20 | Number of batteries required depends on the flight time requirements. Please consult the paper. Also make sure to brwose FastTech catelogue for there maybe new batteries that are better. | https://www.fasttech.com/products/0/10004182/2535100-authentic-lg-18650hg2-3-6v-3000mah-rechargeable
Motor (MN2206) | BLDC motor (type 1) | 4 | 34.00 | 136.00 | Select between MN2206 or MT2208 motors. More details about motors available at T-Motor website | http://www.riseabove.com.au/t-motor-mn2206-13-2000kv
Motor (MT2208) | BLDC motor (type 2) | 4 | 73.00 | 292.00 | Select between MN2206 or MT2208 motors. More details about motors available at T-Motor website | http://www.riseabove.com.au/?rf=kw&kw=T-Motor+MT2208-18+1100KV
T-Motor CF propeller 7x2.4 | CF propeller (type 1) | 2 | 50.00 | 100.00 | Select between 7x2.4 or 8x2.7 propellers. Each pack comes with 2 propellers. One CW and one CCW. | http://www.riseabove.com.au/products/t-motor-propeller-07-2-4.html
T-Motor CF propeller 8x2.7 | CF propeller (type 2) | 2 | 55.00 | 110.00 | Select between 7x2.4 or 8x2.7 propellers. Each pack comes with 2 propellers. One CW and one CCW. | http://www.riseabove.com.au/products/t-motor-propeller-07-2-4.html
20A ESC with Simonk Firmware (2-4S) | Electronic Speed Controllers for Motors | 4 | 18.00 | 72.00 | These ESCs are over provisioned for the motor+prop combinations. You could potentially save a bit on weight and cost by opting for a lower spec ESC. | http://www.riseabove.com.au/dys-sn20a-mini-20a-opto-esc-with-simonk-2-4s
Quadcopter PDB | power distribution board | 1 | 6.00 | 6.00 | There are plenty of options available for this one. Make sure to look around for something that matches with your battery and motor connectors
Avionics
Pixhawk | Autopilot | 1 | 210.00 | 210.00 |  | https://store.3drobotics.com/products/3dr-pixhawk
Telemetry Radio | For sending telemetry data between the GSC and Pixhawk | 1 | 140.00 | 140.00 | Optional but recommended | https://store.3drobotics.com/products/3dr-radio-set
Odroid U3 | On-board companion computer | 1 | 100.00 | 100.00 | U3 has been discontinued by Hardkernel. The replacement is Odroid-XU4. If you are interfacing the XU4 to the Pixhawk, you may need to redesign the level-converter board provided in the Github repo. | http://www.hardkernel.com/main/products/prdt_info.php?g_code=G138745696275&tab_idx=1
Point Grey Firefly FMVU-03MTM-CS | On-board camera | 1 | 385.00 | 385.00 | Resoultion: 640x480, Max FPS:60(in continuous trigger mode only), Monochrome, Global shutter, External trigger | https://www.ptgrey.com/firefly-mv-03-mp-mono-usb-20-micron-mt9v022
Camera GPIO cable | 7 pins, 0.1m GPIO Cable, JST Connector | 1 | 14.00 | 14.00 | Only required if you plan to externally trigger the camera using the level converter board | https://www.ptgrey.com/7-pin-prewired-gpio-jst-connector-3
Boowon BW38BLF, 4mm, 1/3", M12 mount Lens | Lens for Point Grey Firefly | 1 | 14.00 | 14.00 | also available in 6mm and 8mm focal lengths | https://www.ptgrey.com/lenses-m12-micro-lens-4mm
CS to M12 Microlens Adapter | Lens moount for Point Grey Firefly | 1 | 7.00 | 7.00 |  | https://www.ptgrey.com/cs-to-m12-microlens-adaptor-3

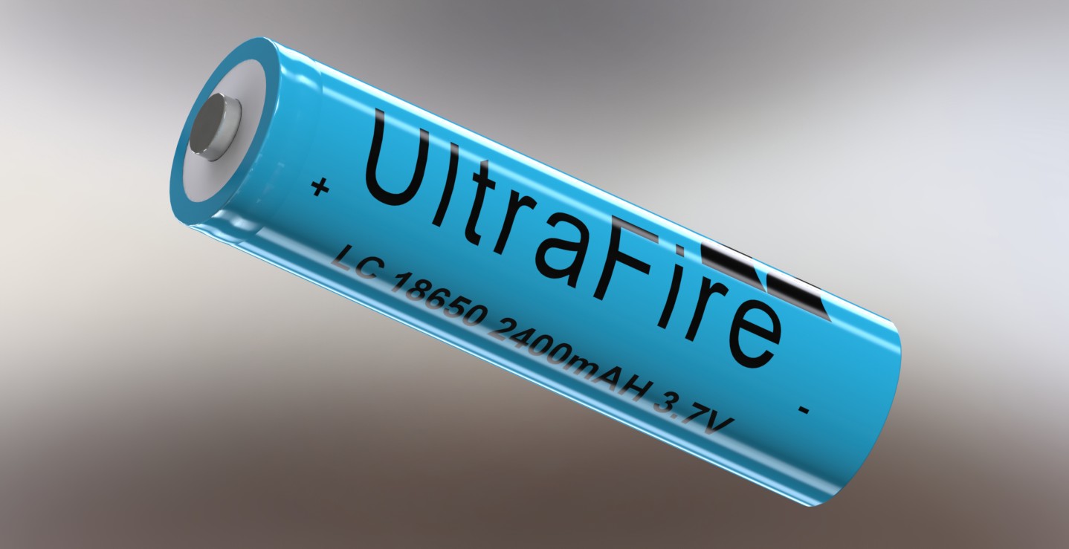
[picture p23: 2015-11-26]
Hardware/Frame/CAD/Parts/ultrafire-18650-2400mah-batteries-1/18650LithiumBatt_Render1.JPG

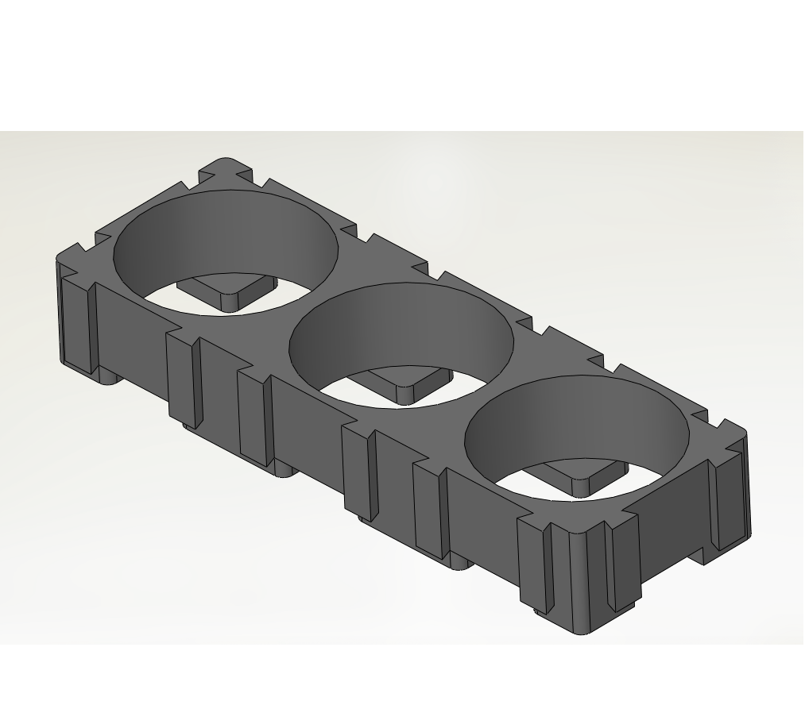
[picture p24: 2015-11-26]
Hardware/Frame/CAD/Parts/3p-18650-battery-bracket-1/Renderings/3p 4.bmp

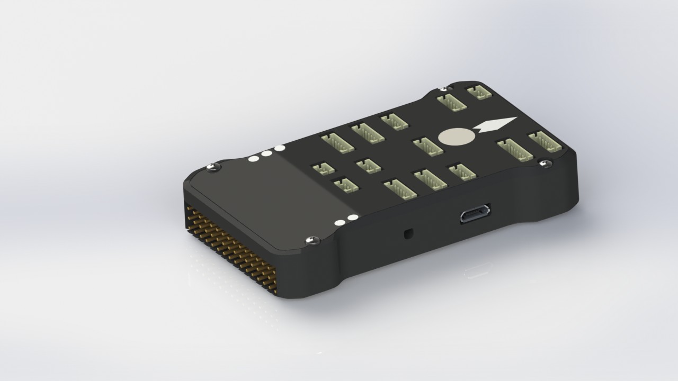
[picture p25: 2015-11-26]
Hardware/Frame/CAD/Parts/Pixhawk/pixhawk1.JPG

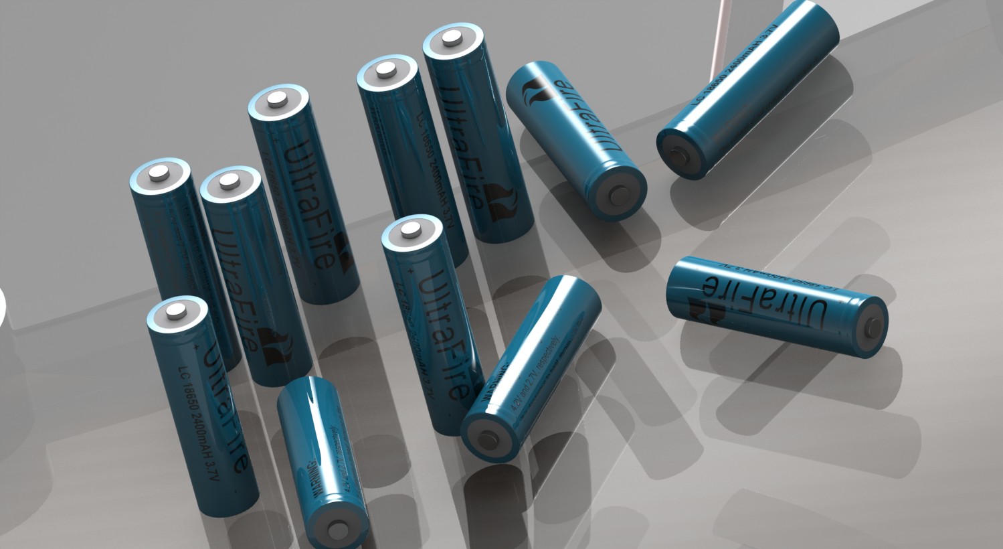
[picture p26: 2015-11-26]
Hardware/Frame/CAD/Parts/ultrafire-18650-2400mah-batteries-1/18650LithiumBatt_Render6.JPG

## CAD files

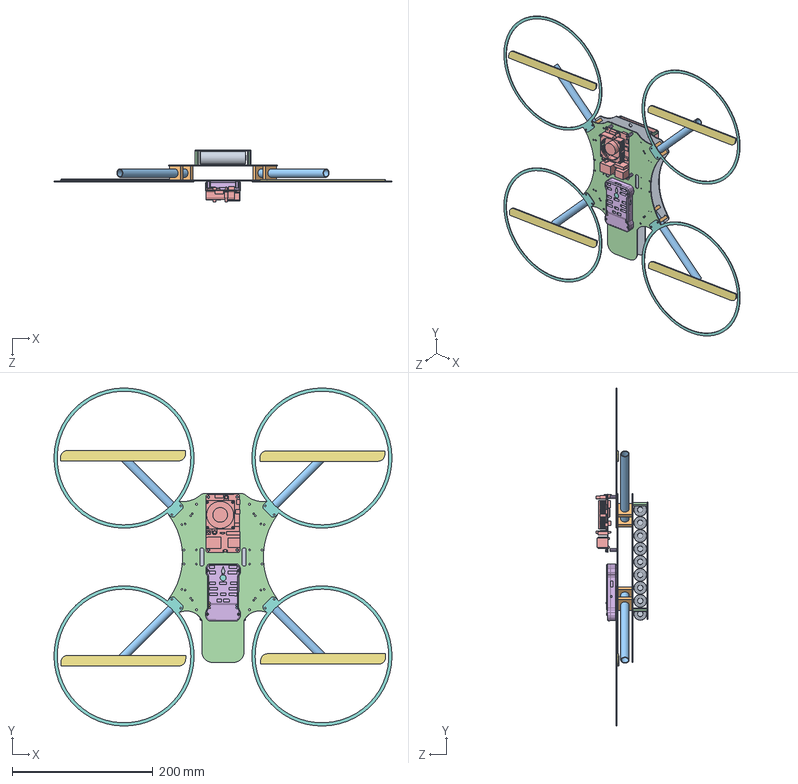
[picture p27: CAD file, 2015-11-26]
Hardware/Frame/CAD/Assem1 45 Degree.SLDASM
480.6 x 480.6 x 73.2 mm
Falcon Level 1 V2
Clamp 12mm x 8
12mm Tube x 4
Falcon Level 2 V2
Odroid_U3
Pixhawk APM
pan head cross recess screw_iso x 4
pièce10
pièce11
Pièce12
Pièce13
Extention 20mm x 4
Falcon Sub Level V2
Extention 10mm x 4
Prop size x 4
Prop Guards x 4
18650 battery x 9

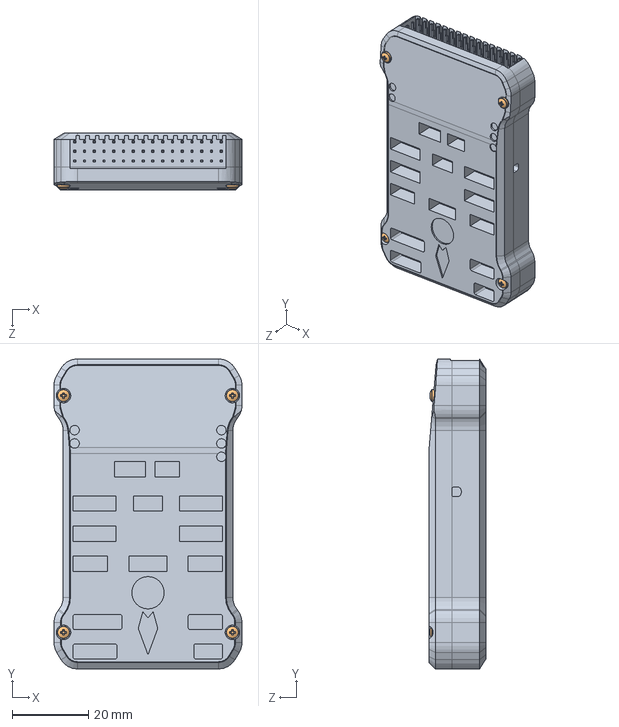
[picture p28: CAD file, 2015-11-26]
Hardware/Frame/CAD/Parts/Pixhawk.SLDASM
49.3 x 81.3 x 15.0 mm
Pixhawk APM
pan head cross recess screw_iso x 4

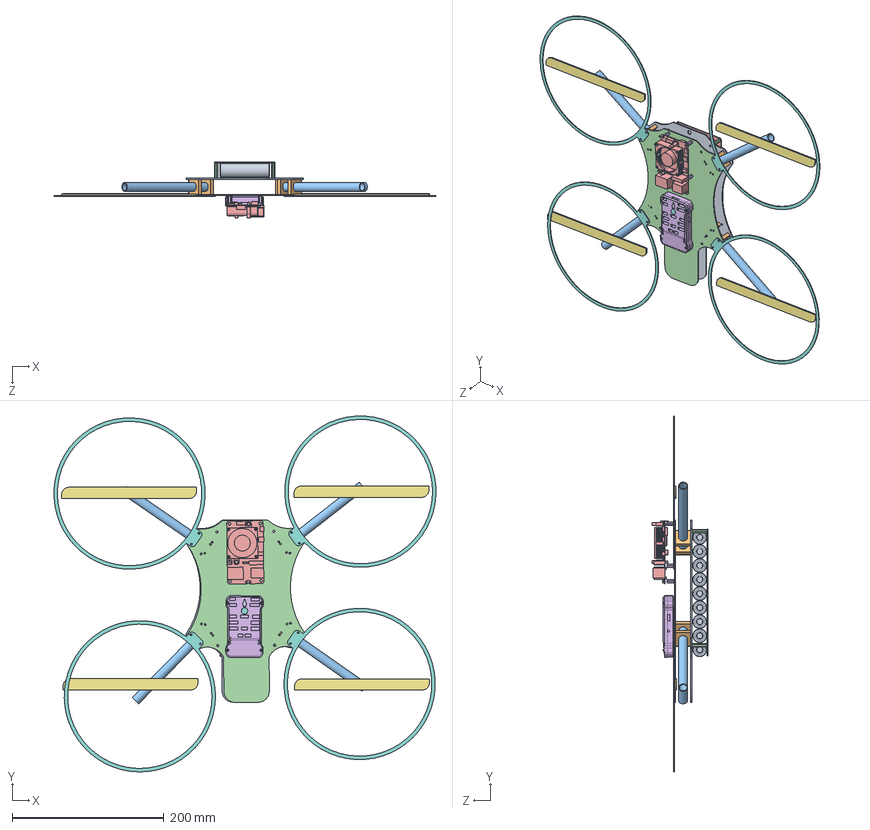
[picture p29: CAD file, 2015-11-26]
Hardware/Frame/CAD/Assem1 35 Degree.SLDASM
503.1 x 468.7 x 73.2 mm
Falcon Level 1 V2
Clamp 12mm x 8
12mm Tube x 4
Falcon Level 2 V2
Odroid_U3
Pixhawk APM
pan head cross recess screw_iso x 4
pièce10^Pixhawk
pièce11^Pixhawk
Pièce12^Pixhawk
Pièce13^Pixhawk
Extention 20mm x 4
Falcon Sub Level V2
Extention 10mm x 4
Prop size x 4
Prop Guards x 4
18650 battery x 9

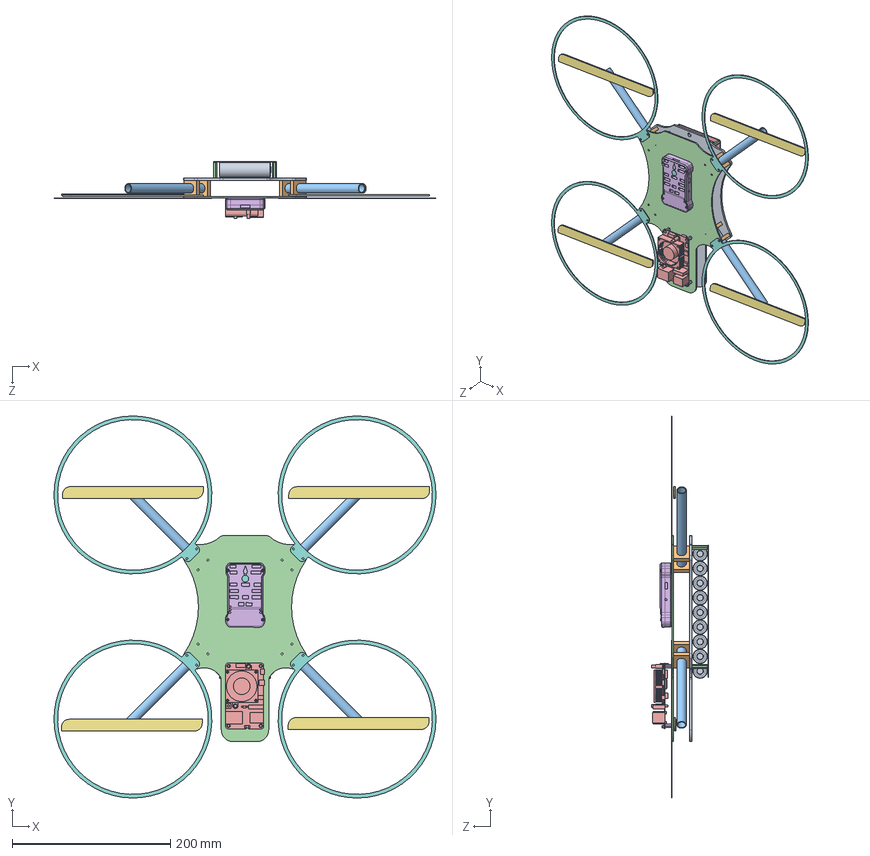
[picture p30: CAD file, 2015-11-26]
Hardware/Frame/CAD/Assem1.SLDASM
482.1 x 482.1 x 72.1 mm
Falcon Level 1 V2
Clamp 12mm x 8
12mm Tube x 4
Falcon Level 2 V2
Odroid_U3
Pixhawk APM
pan head cross recess screw_iso x 4
pièce10^Pixhawk
pièce11^Pixhawk
Pièce12^Pixhawk
Pièce13^Pixhawk
Extention 20mm x 4
Falcon Sub Level V2
Extention 10mm x 4
Prop size x 4
Prop Guards x 4
18650 battery x 9

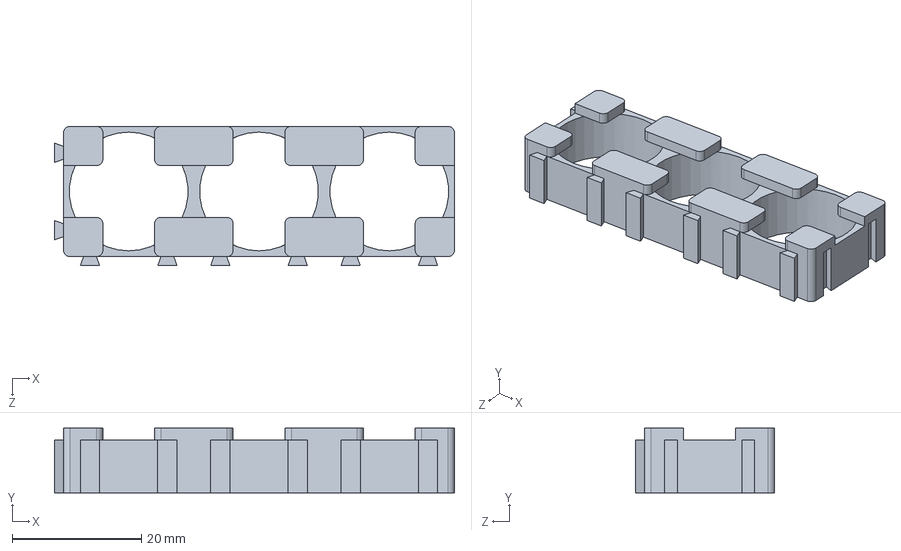
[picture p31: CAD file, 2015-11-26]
Hardware/Frame/CAD/Parts/3p-18650-battery-bracket-1/3P Holder.SLDPRT
62.0 x 10.0 x 21.6 mm

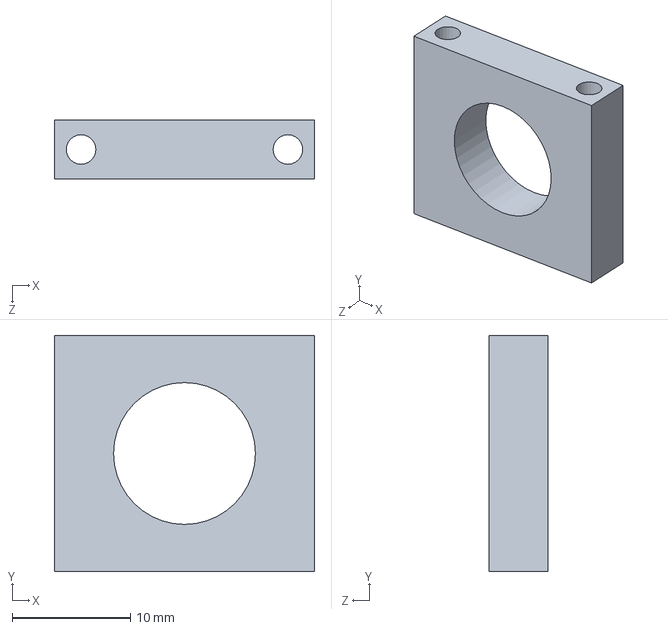
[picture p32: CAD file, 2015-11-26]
Hardware/Frame/CAD/Parts/Chassis/Clamp 12mm.SLDPRT
22.0 x 20.0 x 5.00 mm

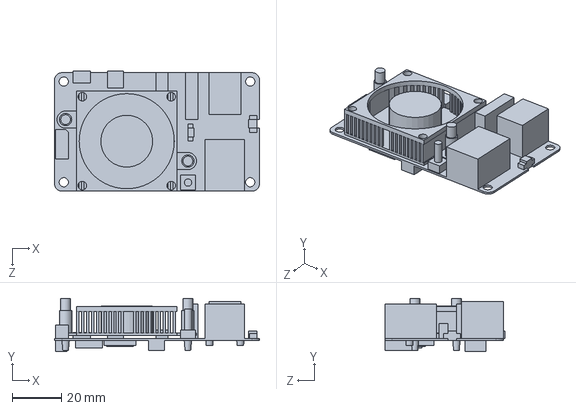
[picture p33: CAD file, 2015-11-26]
Hardware/Frame/CAD/Parts/Odroid U3/Odroid_U3.SLDPRT
83.0 x 21.5 x 48.8 mm

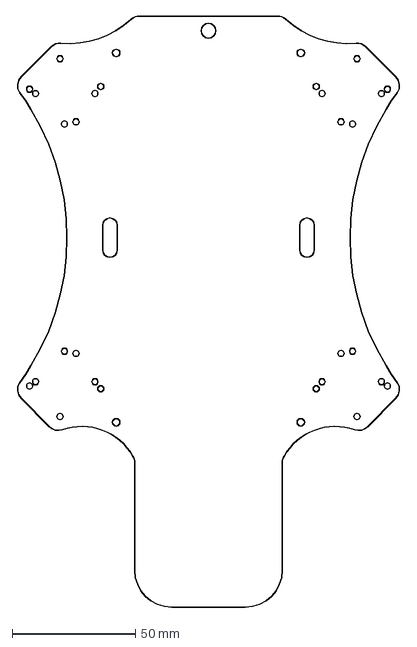
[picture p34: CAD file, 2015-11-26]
Hardware/Frame/Drawings/Falcon Level 1 V3.DXF
156.1 x 240.0 mm

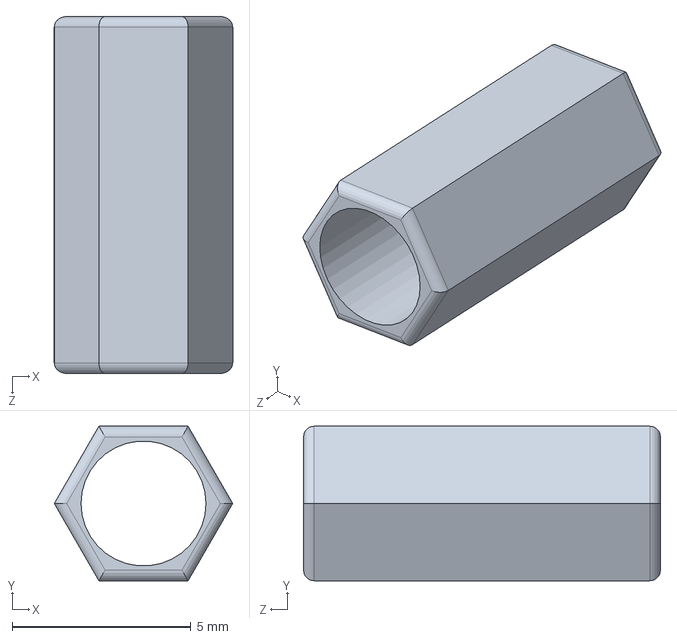
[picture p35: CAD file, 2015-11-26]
Hardware/Frame/CAD/Parts/Chassis/Extention 10mm.SLDPRT
5.00 x 4.33 x 10.0 mm

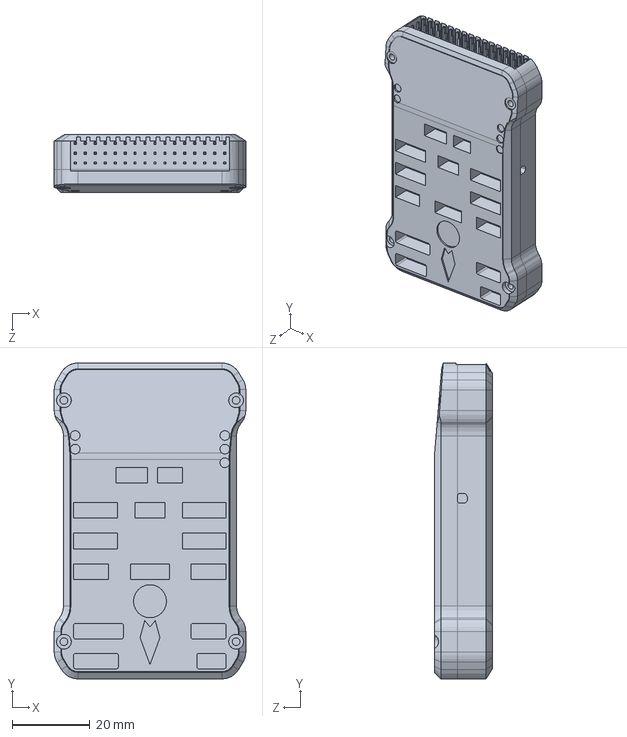
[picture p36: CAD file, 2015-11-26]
Hardware/Frame/CAD/Parts/Pixhawk APM.SLDPRT
49.3 x 81.3 x 15.0 mm

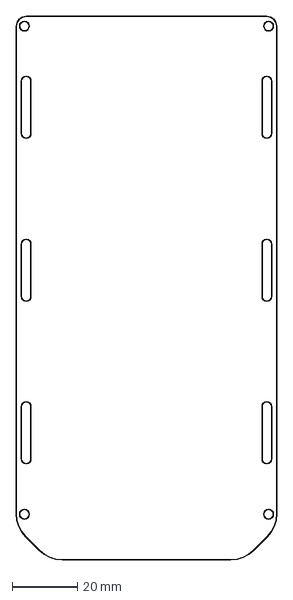
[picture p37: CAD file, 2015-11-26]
Hardware/Frame/Drawings/Falcon Sub Level V2.DXF
80.0 x 167.0 mm

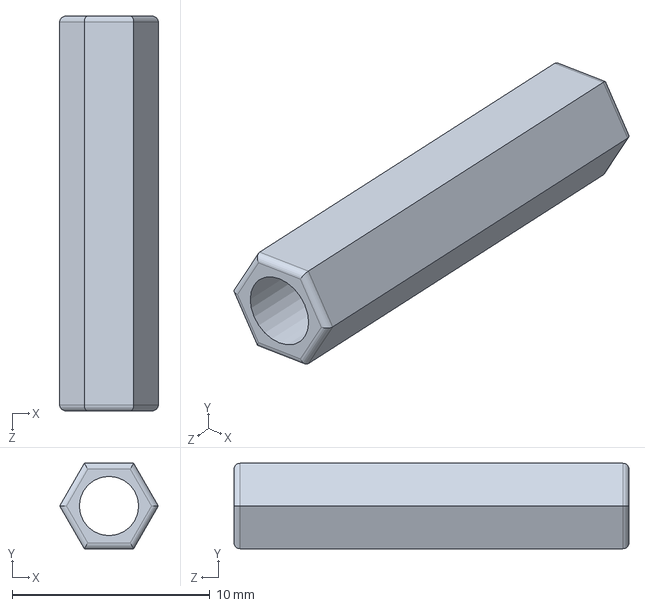
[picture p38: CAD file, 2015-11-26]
Hardware/Frame/CAD/Parts/Chassis/Extention 20mm.SLDPRT
5.00 x 4.33 x 20.0 mm

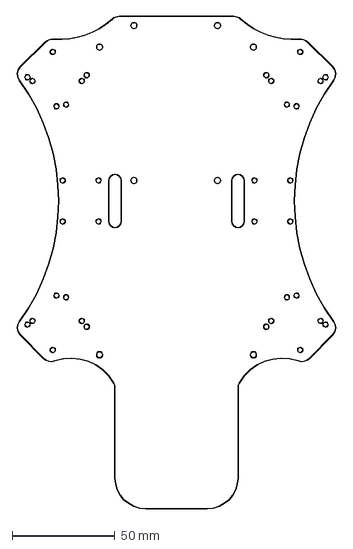
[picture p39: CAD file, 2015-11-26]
Hardware/Frame/Drawings/Falcon Level 2 V3.DXF
156.1 x 240.0 mm

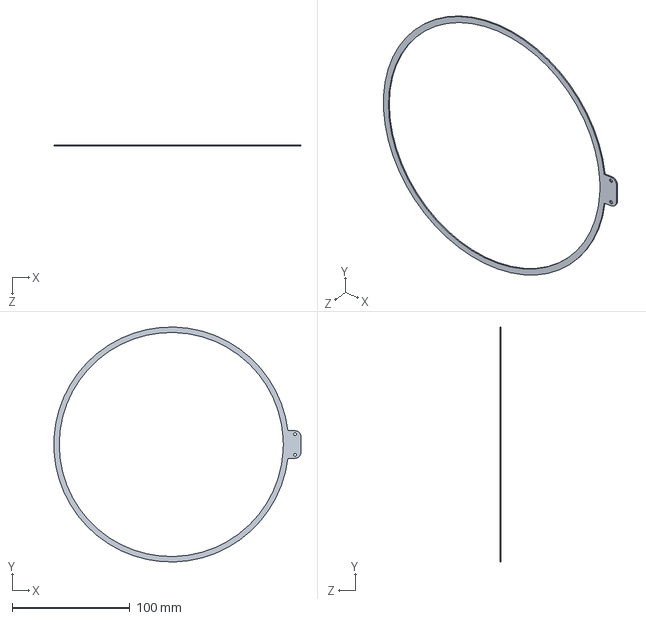
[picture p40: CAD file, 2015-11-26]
Hardware/Frame/CAD/Parts/Chassis/Prop Guards.SLDPRT
209.4 x 199.2 x 1.00 mm

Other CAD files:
Hardware/Frame/CAD/Parts/18650-li-battery/pièce10.sldprt
Hardware/Frame/CAD/Parts/18650-li-battery/Pièce12.sldprt
Hardware/Frame/CAD/Parts/18650-li-battery/pièce11.sldprt
Hardware/Frame/CAD/Parts/18650-li-battery/Pièce13.sldprt
Hardware/Frame/CAD/Parts/18650-li-battery/18650 battery.SLDPRT
Hardware/Frame/CAD/Parts/18650-li-battery/18650 battery.stl
Hardware/Frame/CAD/Parts/Chassis/12mm Tube.SLDPRT
Hardware/Frame/CAD/Parts/Chassis/Falcon Level 1 V1.SLDPRT
Hardware/Frame/CAD/Parts/Chassis/Falcon Level 1 V2.SLDPRT
Hardware/Frame/CAD/Parts/Chassis/Falcon Level 1 square V2.SLDPRT
Hardware/Frame/CAD/Parts/Chassis/Falcon Level 2 V2 square edge.SLDPRT
Hardware/Frame/CAD/Parts/Chassis/Falcon Level 2 V2.SLDPRT
Hardware/Frame/CAD/Parts/Chassis/Falcon Level 2 square V2.SLDPRT
Hardware/Frame/CAD/Parts/Chassis/Falcon Sub Level V2.SLDPRT
Hardware/Frame/CAD/Parts/Chassis/Prop size.SLDPRT

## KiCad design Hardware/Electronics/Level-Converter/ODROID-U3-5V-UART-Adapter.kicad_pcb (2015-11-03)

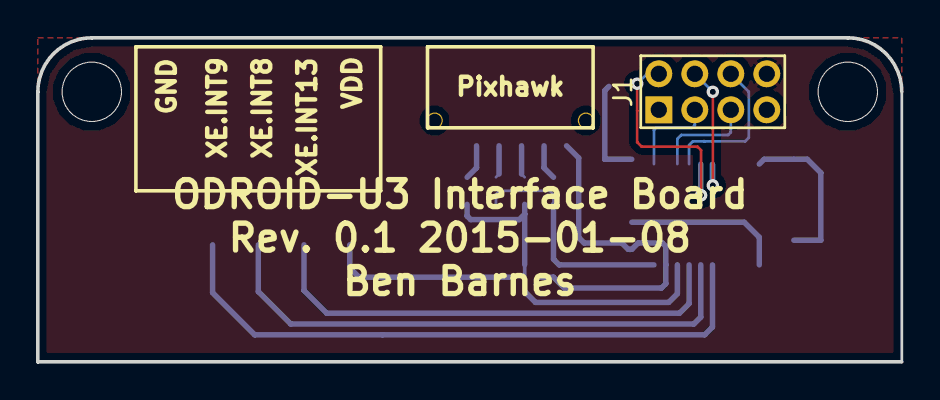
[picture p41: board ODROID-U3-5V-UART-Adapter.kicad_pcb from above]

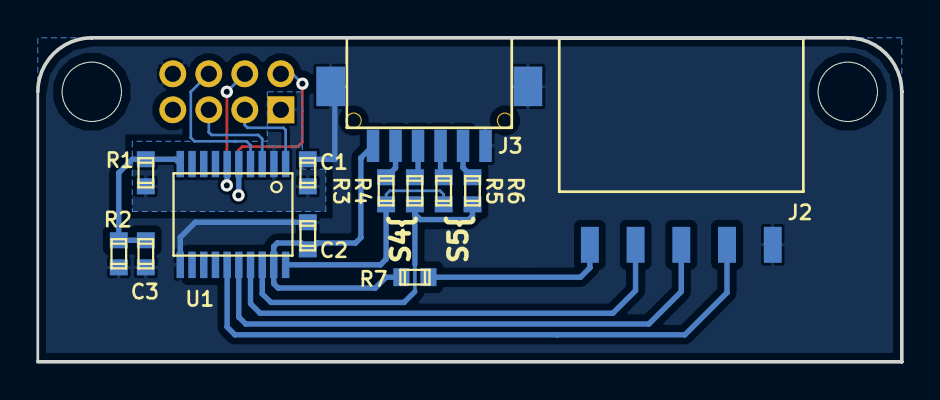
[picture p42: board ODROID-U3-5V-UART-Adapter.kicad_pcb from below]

Board: 2 copper layers, 48.0 x 18.0 mm, 16 parts (13 on the bottom side), 19 nets.

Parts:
C1, C2: 10n; c_0603
C3: 1n; c_0603
J1: PIN_HEADER_2X4_2MM_TH; PIN_ARRAY_2MM_4x2
J2: BG300-05-A-L-A
J3: DF13-6P-1.25H
M1, M2: M3_DRILL
R1: 1k; c_0603
R2: 100k; c_0603
R3, R4, R5, R6, R7: 0R; c_0603
U1: TXS0108EPWR; tssop-20

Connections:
+1.8V: C1.1, J1.1, R1.1, U1.2
/PIXHAWK_S4_RX: J3.3, R4.2
/PIXHAWK_S4_TX: J3.2, R3.2
/PIXHAWK_S5_RX: J3.5, R6.2
/PIXHAWK_S5_TX: J3.4, R5.2
/VDD_CONN: J2.1, R7.2
GND: C1.2, C2.2, C3.2, J1.8, J2.5, J3.6, J3.7, J3.8, R2.1, U1.11
GPIO1: J2.2, U1.17
GPIO2: J2.3, U1.16
GPIO3: J2.4, U1.15
OE: C3.1, R1.2, R2.2, U1.10
PIXHAWK_RX: R4.1, R6.1, U1.18
PIXHAWK_TX: R3.1, R5.1, U1.20
UART_0.RXD: J1.3, U1.1
UART_0.TXD: J1.5, U1.3
VDD: C2.1, J3.1, R7.1, U1.19
XE.INT8: J1.2, U1.5
XE.INT9: J1.4, U1.6
XE.INT13: J1.6, U1.4

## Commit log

2015-11-03 Added level converter design files.
    [ODROID-U3-5V-UART-Adapter.kicad_pcb, ODROID-U3-5V-UART-Adapter.sch]
2015-11-06 Added frame design
    Added version 1 of the frame design.
    [12mm Tube.SLDPRT, Assem1.SLDASM, Clamp 12mm.SLDPRT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]
2015-11-12 removing old solidworks files
    [12mm Tube.SLDPRT, Assem1.SLDASM, Clamp 12mm.SLDPRT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]
2015-11-12 Added up to date solidworks and autocad models for the frame and required components
    [12mm Tube.SLDPRT, 18650 battery.SLDPRT, 18650 battery.stl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]
2015-11-26 adding the parts list files
    [Parts list.csv, Parts list.xlsx]
2015-11-26 adding information about KiCad
